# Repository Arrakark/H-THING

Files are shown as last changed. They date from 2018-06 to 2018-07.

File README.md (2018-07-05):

# H-THING

An H-Bridge circuit for controlling a single robot motor.

## PCB Description

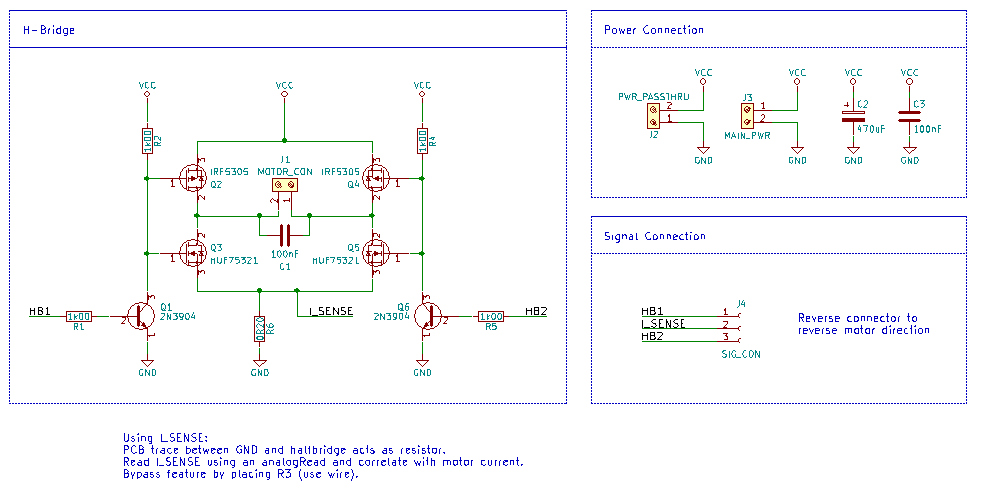
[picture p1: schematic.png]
Schematic


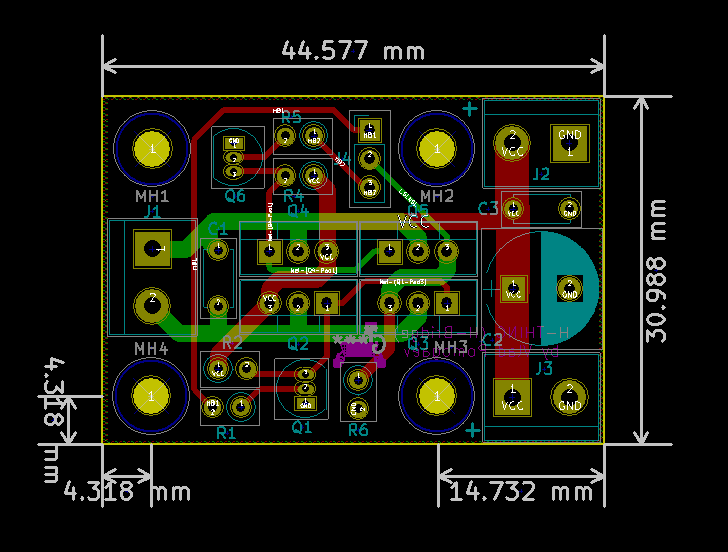
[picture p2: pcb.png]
PCB


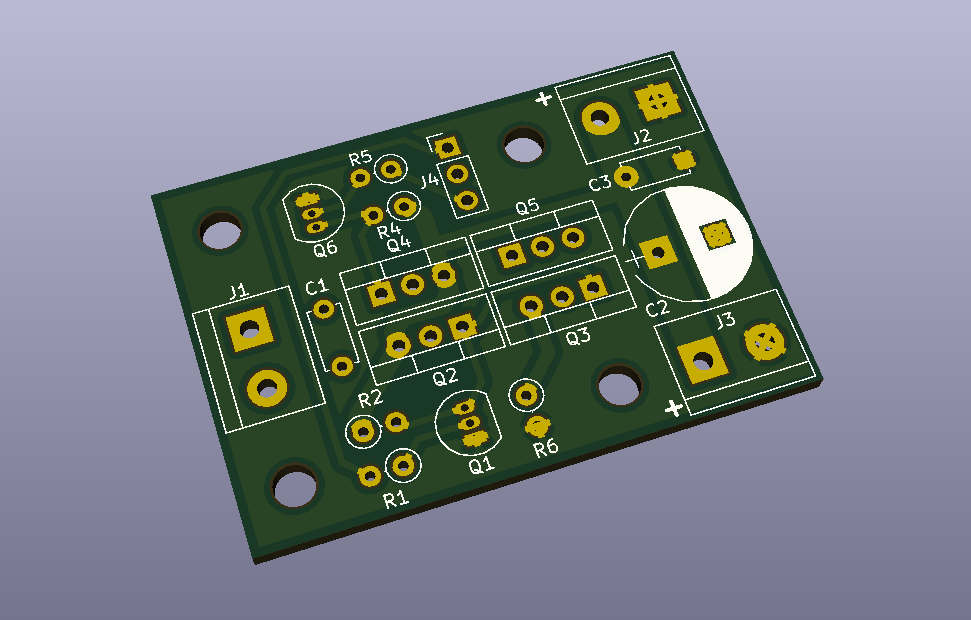
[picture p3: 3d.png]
3d view


### Specs

* 5V - 17V motor voltage range
* To be used with <1000Hz switching freqnuency (500Hz is preferred)
* Supports 3.3v and 5.0v logic level inputs
* Capable of driving up to 3A
* Requires only one PWM pin for speed, one digial I/O for direction
* Can be used as a half-bridge if direction pin is disconnected
* Has space for a current-sensing resistor (R6)
* **Cannot be used to coast the motor**

This project was created using KiCad 5 RC2. Use it to open and edit this design.

### BOM

| "Id" | "Designator" | "Package" | "Quantity" | "Designation" | "Supplier and ref" |  |  | 
|---|---|---|---|---|---|--|--|
| 1 | "MH3,MH2,MH4,MH1" | "MountingHole_3.2mm_M3" | 4 | "MountingHole_3.2mm_M3" | |  |  | 
| 2 | "C1,C3" | "C_Disc_D5.0mm_W2.5mm_P5.00mm" | 2 | "100nF" | |  |  | 
| 3 | "C2" | "CP_Radial_D10.0mm_P5.00mm" | 1 | "470uF" | |  |  | 
| 4 | "J1" | "TerminalBlock_bornier-2_P5.08mm" | 1 | "MOTOR_CON" | |  |  | 
| 5 | "J2" | "TerminalBlock_bornier-2_P5.08mm" | 1 | "PWR_PASSTHRU" | |  |  | 
| 6 | "J3" | "TerminalBlock_bornier-2_P5.08mm" | 1 | "MAIN_PWR" | |  |  | 
| 7 | "Q1,Q6" | "TO-92_Inline_Narrow_Oval" | 2 | "2N3904" | |  |  | 
| 8 | "R1,R2,R4,R5" | "R_Axial_DIN0207_L6.3mm_D2.5mm_P2.54mm_Vertical" | 4 | "1k00" | |  |  | 
| 9 | "J4" | "Socket_Strip_Straight_1x03_Pitch2.54mm" | 1 | "SIG_CON" | |  |  | 
| 10 | "Q2,Q4" | "TO-220-3_Vertical" | 2 | "IRF5305" | |  |  | 
| 11 | "Q3,Q5" | "TO-220-3_Vertical" | 2 | "HUF75321" | |  |  | 
| 12 | "R6" | "R_Axial_DIN0207_L6.3mm_D2.5mm_P2.54mm_Vertical" | 1 | "0R20" | |  |  | 
| 13 | "G***" | "rover" | 1 | "LOGO" | |  |  | 

## Installing

Install the H-THING using standoffs on the robot. Apply motor power (5-17V) to the screw terminals on the right hand side. **Make sure the polarity is correct!** The other screw terminal is for power pass-trough. Use the passthrough to chain more H-THINGs together. Finally, connect the motor to the last screw terminal (the one with the motor label).

Connect the H-THING to a microcontroller by connecting one of the outermost pins to a PWM pin, and the other to a digital I/O (non PWM).

## Signal Control

Use the library included with this repo to control the speed and direction of the motor. 

Use the following code to create a H-THING object:
```
#define SPEED_PIN 9 
#define DIR_PIN 3 
HTHING leftm = HTHING(PA3,PA2);
```
To control the motor:
```
left_motor.stop(); //stops the motor
left_motor.run(-255); //runs the motor backwards
left_motor.run(120); //runs the motor forwards
```

## License

This project is licensed under the MIT License - see the [LICENSE.md](https://github.com/Arrakark/H-THING/blob/master/LICENSE) file for details

## Acknowledgments

* Special thanks to the V2FC robot team!

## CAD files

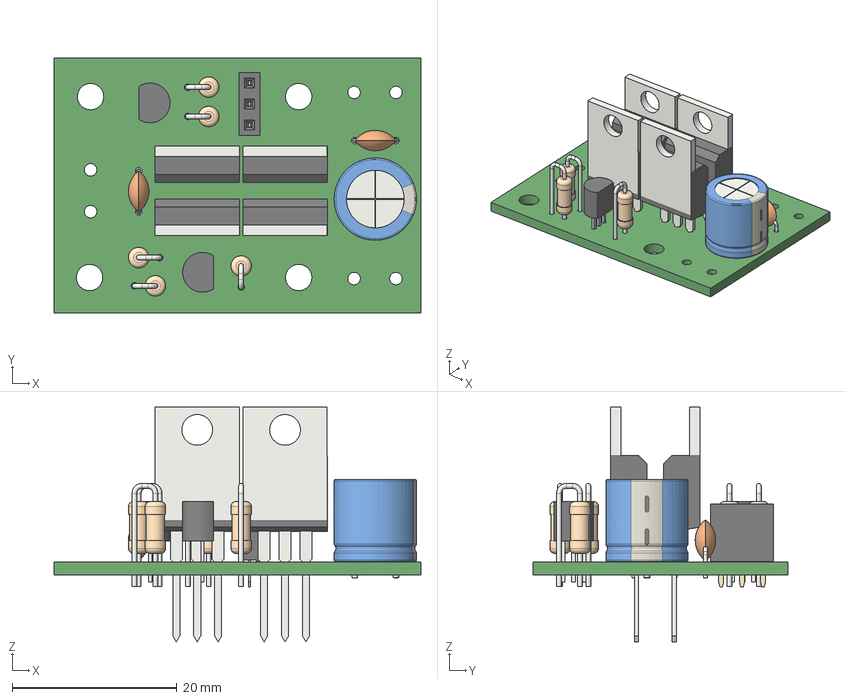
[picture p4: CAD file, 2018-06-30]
H-THING.step
44.6 x 31.0 x 28.5 mm

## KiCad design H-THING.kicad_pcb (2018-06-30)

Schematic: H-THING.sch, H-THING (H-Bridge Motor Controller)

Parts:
C1, C3: 100nF; C_Disc_D5.0mm_W2.5mm_P5.00mm
C2: 470uF; CP_Radial_D10.0mm_P5.00mm
J1: MOTOR_CON; TerminalBlock_bornier-2_P5.08mm
J2: PWR_PASSTHRU; TerminalBlock_bornier-2_P5.08mm
J3: MAIN_PWR; TerminalBlock_bornier-2_P5.08mm
J4: SIG_CON; PinSocket_1x03_P2.54mm_Vertical
Q1, Q6: 2N3904; TO-92_Inline
Q2, Q4: IRF5305; TO-220-3_Vertical
Q3, Q5: HUF75321; TO-220-3_Vertical
R1, R2, R4, R5: 1k00; R_Axial_DIN0207_L6.3mm_D2.5mm_P2.54mm_Vertical
R6: 0R20; R_Axial_DIN0207_L6.3mm_D2.5mm_P2.54mm_Vertical

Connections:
/HB1: J4.1, R1.2
/HB2: J4.3, R5.1
/I_SENSE: J4.2, Q3.3, Q5.3, R6.1
GND: C2.2, C3.2, J2.1, J3.2, Q1.1 (E), Q6.1 (E), R6.2
unnamed: C1.1, J1.1, Q4.2, Q5.2
unnamed: C1.2, J1.2, Q2.2, Q3.2
unnamed: Q1.2 (B), R1.1
unnamed: Q1.3 (C), Q2.1, Q3.1, R2.2
unnamed: Q4.1, Q5.1, Q6.3 (C), R4.2
unnamed: Q6.2 (B), R5.2
VCC: C2.1, C3.1, J2.2, J3.1, Q2.3, Q4.3, R2.1, R4.1

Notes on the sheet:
H-Bridge
Power Connection
Signal Connection
Using I_SENSE: PCB trace between GND and halfbridge acts as resistor. Read I_SENSE using an analogRead and correlate with motor current. Bypass feature by placing R3 (use wire).
Reverse connector to reverse motor direction

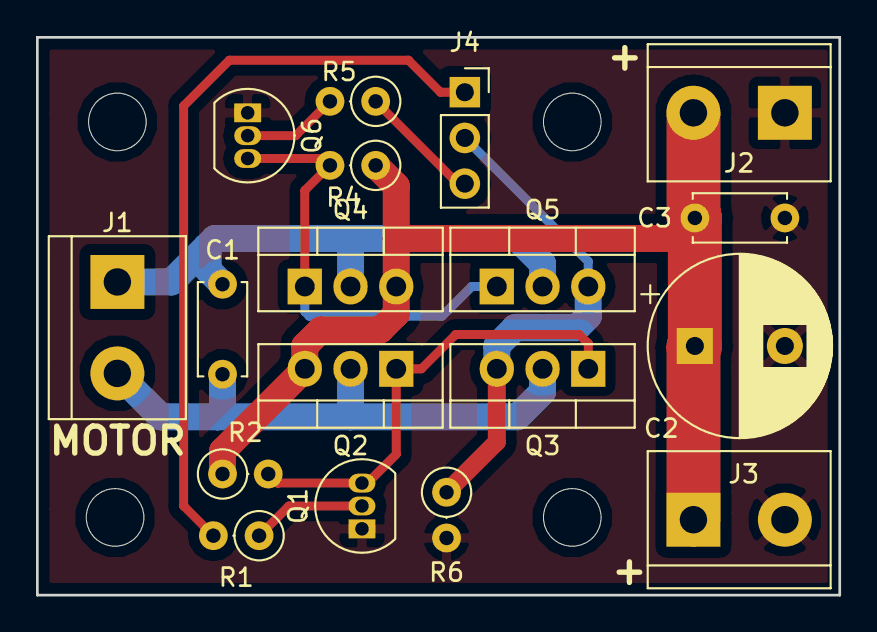
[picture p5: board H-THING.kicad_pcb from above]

Board: 2 copper layers, 44.6 x 31.0 mm, 22 parts (0 on the bottom side), 11 nets.

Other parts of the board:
MH1, MH2, MH3, MH4: MountingHole_3.2mm_M3

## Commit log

2018-06-08 Finished schematic, started PCB
    [H-THING.kicad_pcb]
2018-06-08 Layed out PCB
    [H-THING.kicad_pcb, _saved_H-THING.sch]
2018-06-09 Added images
    [H-THING.kicad_pcb, H-THING.sch, _saved_H-THING.sch]
2018-06-09 Added FAB files
    [H-THING-2018-06-08-21-41-00.sch, H-THING.csv, H-THING.kicad_pcb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]
2018-06-12 Added propper grbr outputs
    [H-THING-B.Cu.gbr, H-THING-B.Mask.gbr, H-THING-B.SilkS.gbr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]
2018-06-30 Updated 3d model with components
    [H-THING.kicad_pcb, H-THING.sch, H-THING.step]
